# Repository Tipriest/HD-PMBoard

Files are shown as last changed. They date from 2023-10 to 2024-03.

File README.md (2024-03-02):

### 1.设计要求

1. 尺寸，30.50mm孔距
2. 电源输入: 4S-6S(14-25.2V)
3. 电源输出:
   * 直出/45A 四路
   * 12V/7.5A 一路
   * 5V/5A 一路
4. 将PMU相关的东西进行集成(5V转压+飞控供电+采样电阻+模拟信号)(CAN信号先留着，下一版再说)

### 2. 设计要求分析

1. 12V是用来给Nvidia的系列模组供电的，根据目前(2023.11.11)的各个模组的功耗情况，可以得知**Jeston AGX Origin 64GB**需要15W-60W的电源，所以保险起见需要提供12V/7.5A=90W的一路电源 *[Reference](https://www.nvidia.com/en-sg/autonomous-machines/embedded-systems/jetson-orin/)*
2. 5V是用来给飞控供电的，飞控5V/5A 一路

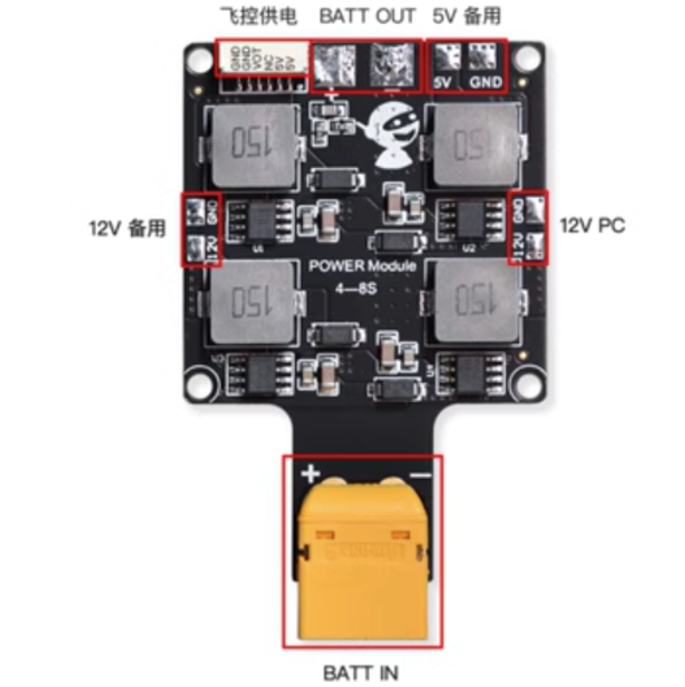
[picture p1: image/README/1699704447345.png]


3. PMU设计分析: PMU在正常情况下是这样的一个模块，其他一些名称有飞行电流计 CAN电流计 *[Reference](https://item.taobao.com/item.htm?spm=a21n57.1.0.0.57e4523cPJaut3&id=620349108685&ns=1&abbucket=3#detail)*

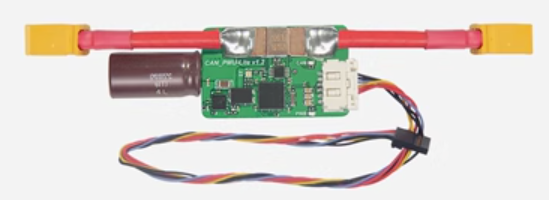
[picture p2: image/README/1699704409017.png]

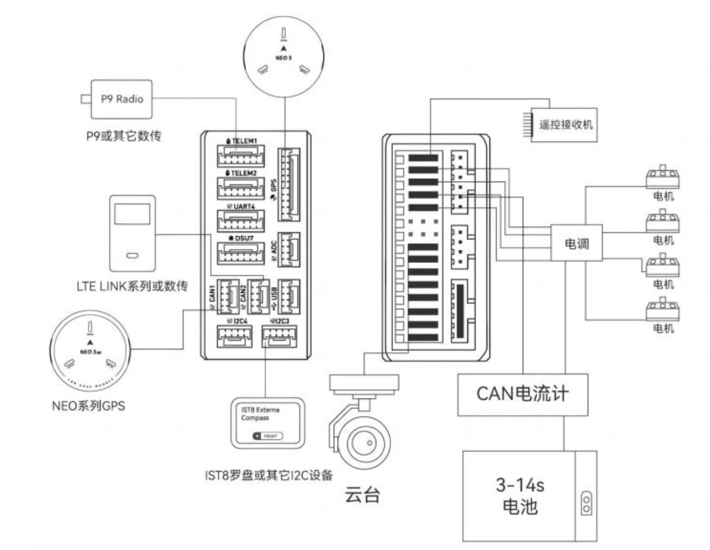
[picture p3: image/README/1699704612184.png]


> * 正常的飞控，以Nora+为例，一般会拥有两个供电的输入端口，称为PowerA和PowerC，根据下图的解释可以知道，PowerA是正常的ADC信息+供电的通道，PowerC是CAN信息+供电的通道
>
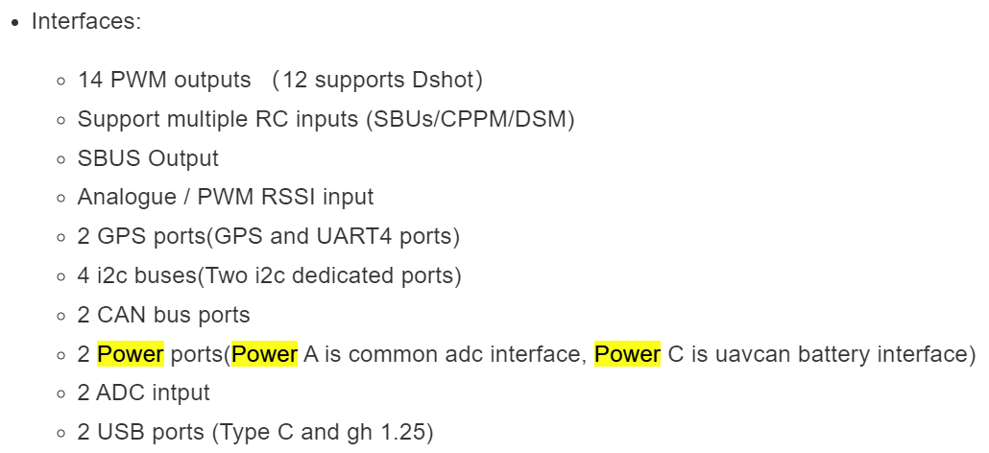
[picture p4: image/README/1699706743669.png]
> 

> * 飞控的电源输入的正常的6pin线序为下图所示，具有VOL和CUR，分别表示输入电压和输入电流
>
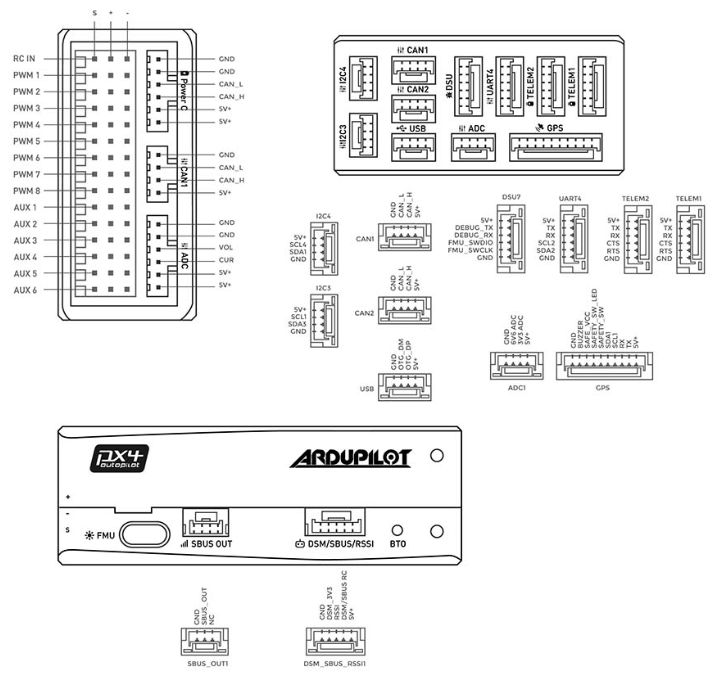
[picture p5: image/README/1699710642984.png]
> 

### 3. 方案选型

> * 采用PowerA端口，提供ADC信息
> * 电流采样: 采用0.25mr采样电阻，采用INA240A3进行100倍增益放大，输出模拟电流采样值，安培/伏特写入40
> * 电压采样: 采用OPA171AIDBVR运放，采样电源的输入电压，电压分压器写入16
>
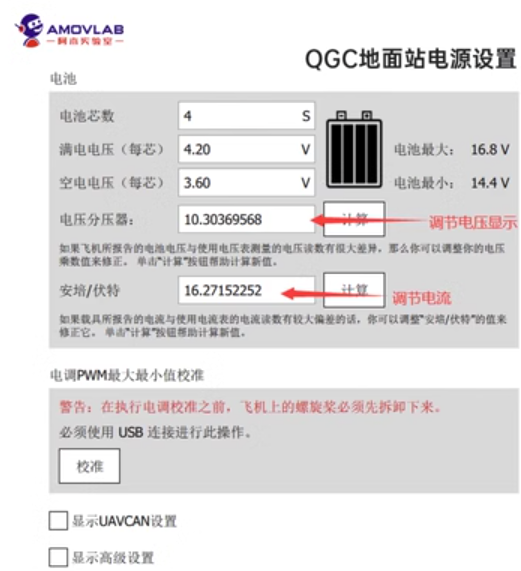
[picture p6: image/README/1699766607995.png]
> 
>
> * 分压器设计采样范围
>
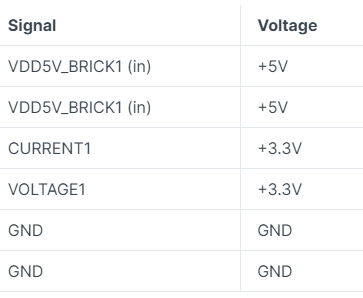
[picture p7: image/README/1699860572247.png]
> 
>
> * 转压芯片选型
>
> | 芯片名称        |      厂家      | 输入电压范围 | 输出电压范围 | 输出电流max |     优缺点     |
> | :-------------- | :------------: | :----------: | :----------: | :---------: | :-------------: |
> | LT8645SIV#PBF   |  ADI(亚德诺)  |   3.4V-65V   |   1.8V~12V   |     8A     |  49.15/片 难焊  |
> | SIC461ED-T1-GE3 |  VISHAY(威世)  |   4.5V-60V   | 800mV~55.2V |     10A     | 14.02/片 正常焊 |
> | SIC471ED-T1-GE3 |  VISHAY(威世)  |   4.5V-55V   | 800mV~50.6V |     12A     | 17.65/片 正常焊 |
> | FAN65008B       | onsemi(安森美) |   4.5V-65V   | 600mV~32.5V |     10A     |  32/片 正常焊  |
>
> * 采用SIC461ED-T1-GE3进行 **输入电压** 转 **12V** ，效率在96-97%
> * 采用SIC461ED-T1-GE3进行 **输入电压** 转 **5V** ，效率在94-95%

### 4.原理图及PCB

#### 4.1 原理图

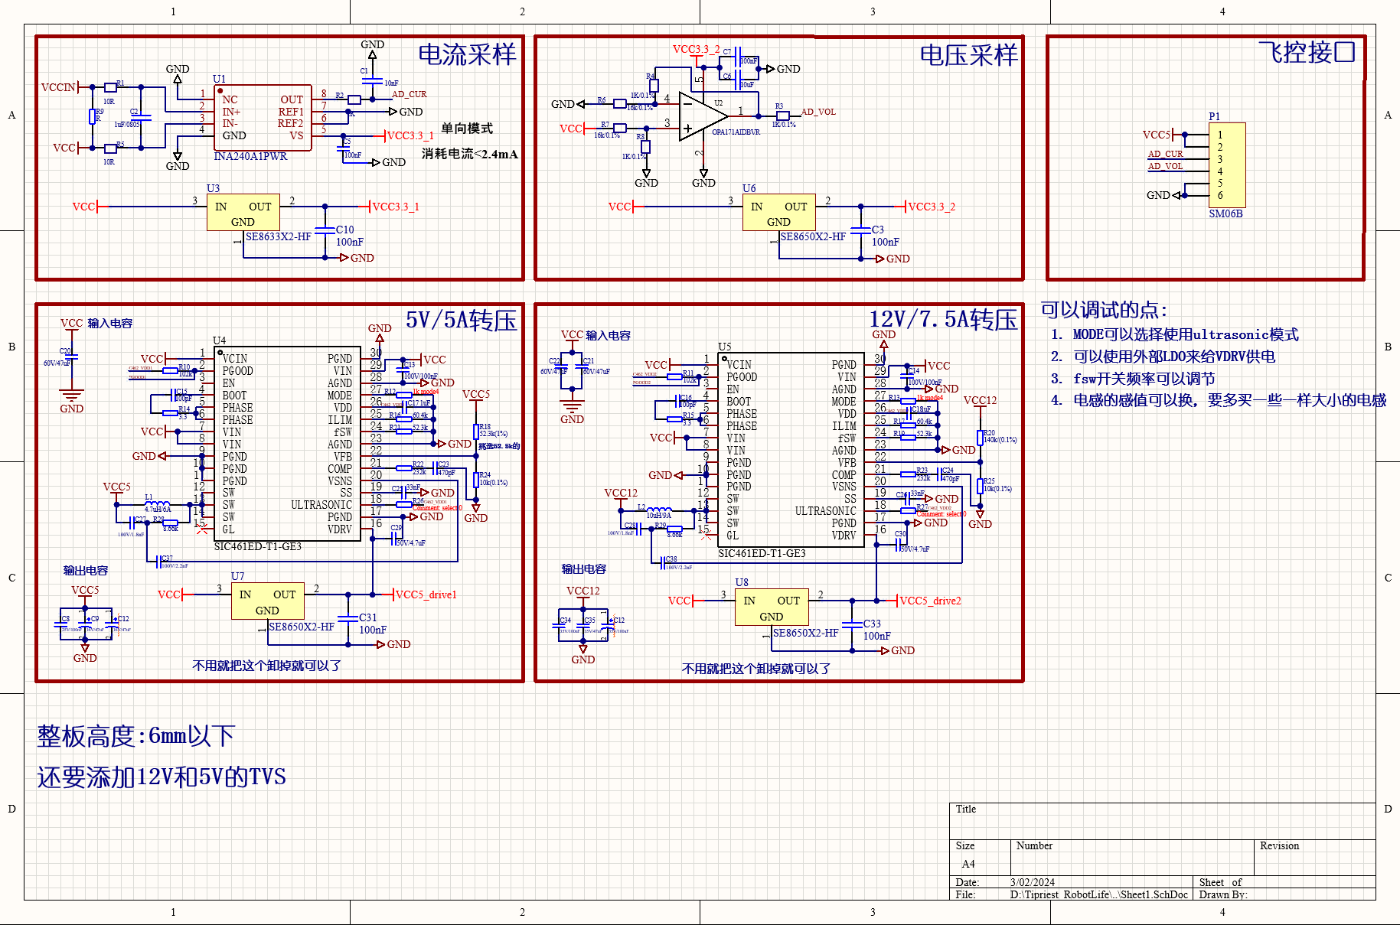
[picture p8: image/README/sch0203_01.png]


#### 4.2 PCB

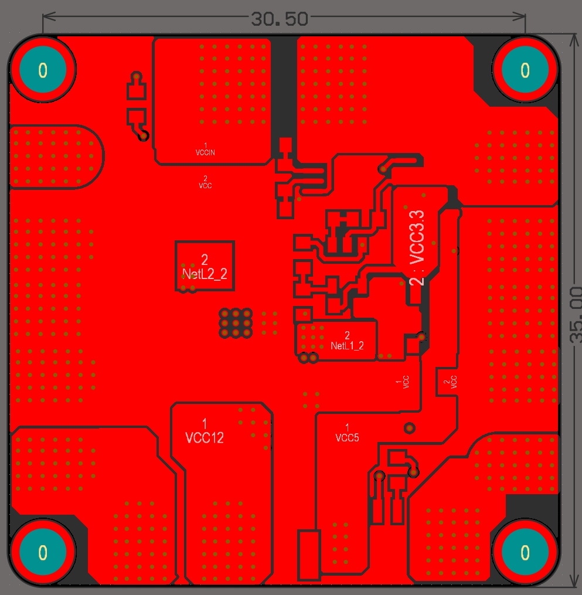
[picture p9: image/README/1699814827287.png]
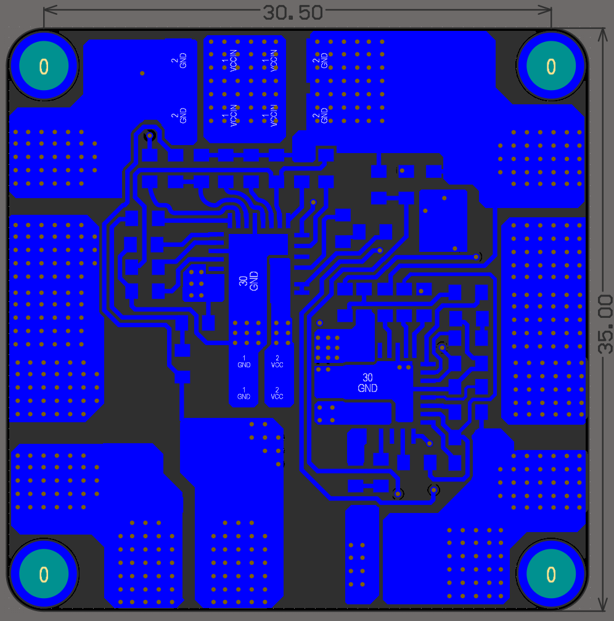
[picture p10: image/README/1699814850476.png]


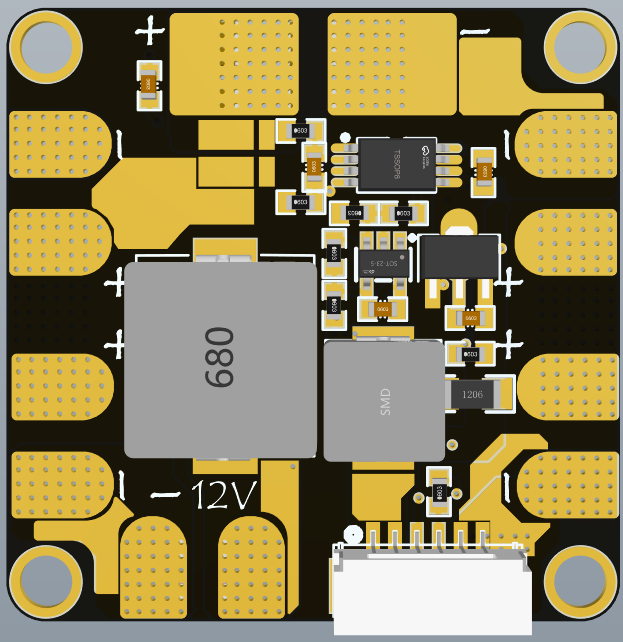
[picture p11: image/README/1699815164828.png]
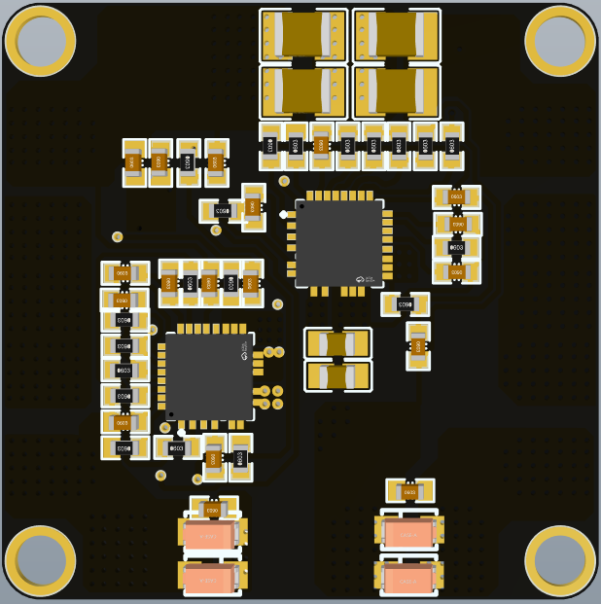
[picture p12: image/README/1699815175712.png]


### 5.待办

1. 12V转压相关的东西还要计算(12V现在的相关参数都是搬的5V的相关参数)
2. 优化一下布局，重新考虑一下布板，现在的大电流相关的东西还需要重新进行考虑
3. 在飞控引脚和12V引脚处加标注
4. 把使用注意事项写到板子的背面

### 6.测试

1. 空载，满载电压准确度
2. 空载，满载电源纹波(在满载的时候纹波在50mV以下)
3. 动态响应度(突然加载和掉载的时候)(在300mV以内可以接受)
4. 发热情况(温度越低越好，满载5min不要高于60度)
5. 效率(任意负载高于96%)
6. 加入输出的12V和5V TVS

### 7.异常测试

1. 镊子输出短路查看响应
2. 开关串联输入查看模块是否会烧毁
3. 动态响应度(突然加载和掉载的时候)(在300mV以内可以接受)
4. 发热情况(温度越低越好，满载5min不要高于50度)
5. 效率(任意负载高于96%)
6. 加入输出的12V和5V TVS

### 8.可能发生的最坏的事情

1. 12V转压故障，导致12V直出电源电压烧坏后级电脑、无人机炸机
2. 飞控6pin引脚线序画反或者接线反导致烧飞控
3. 飞控模拟电压采样出问题烧飞控
4.

### 9.使用注意

1. 5V路禁止同时给舵机或其他电机供电
2. 12V禁止同时给其他舵机或者电机供电
3.

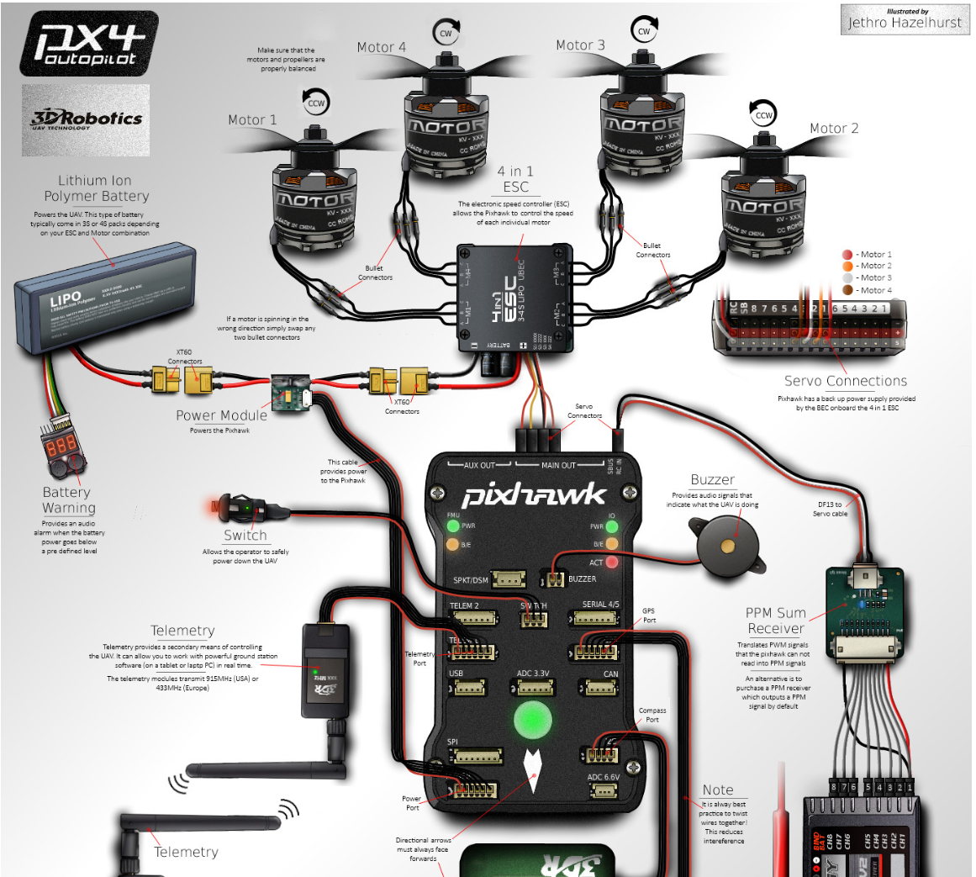
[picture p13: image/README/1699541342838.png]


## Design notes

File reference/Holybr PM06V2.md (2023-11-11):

## Holybr PM06V2

[淘宝链接](https://item.taobao.com/item.htm?spm=a21n57.1.0.0.2a8f523c6srMib&id=584871481169&ns=1&abbucket=3#detail)

#### Chip Used

LM5576 for 5V/3A output

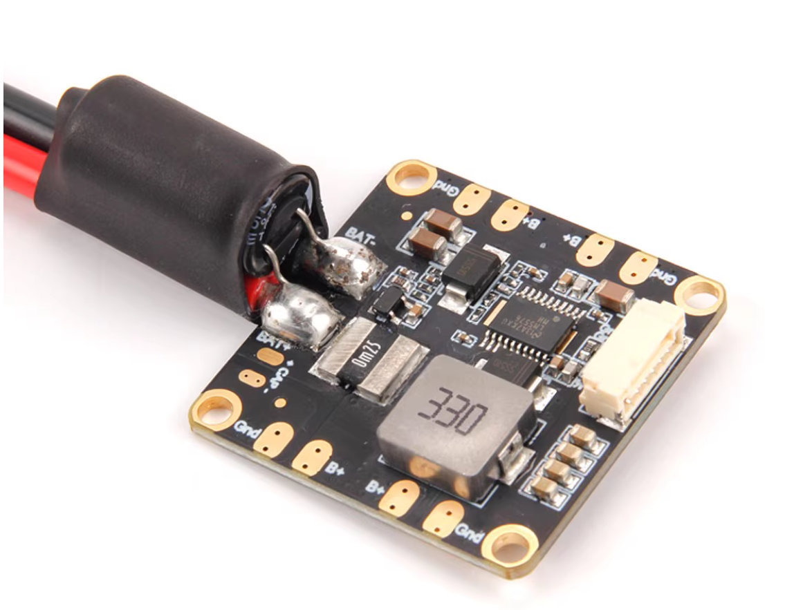
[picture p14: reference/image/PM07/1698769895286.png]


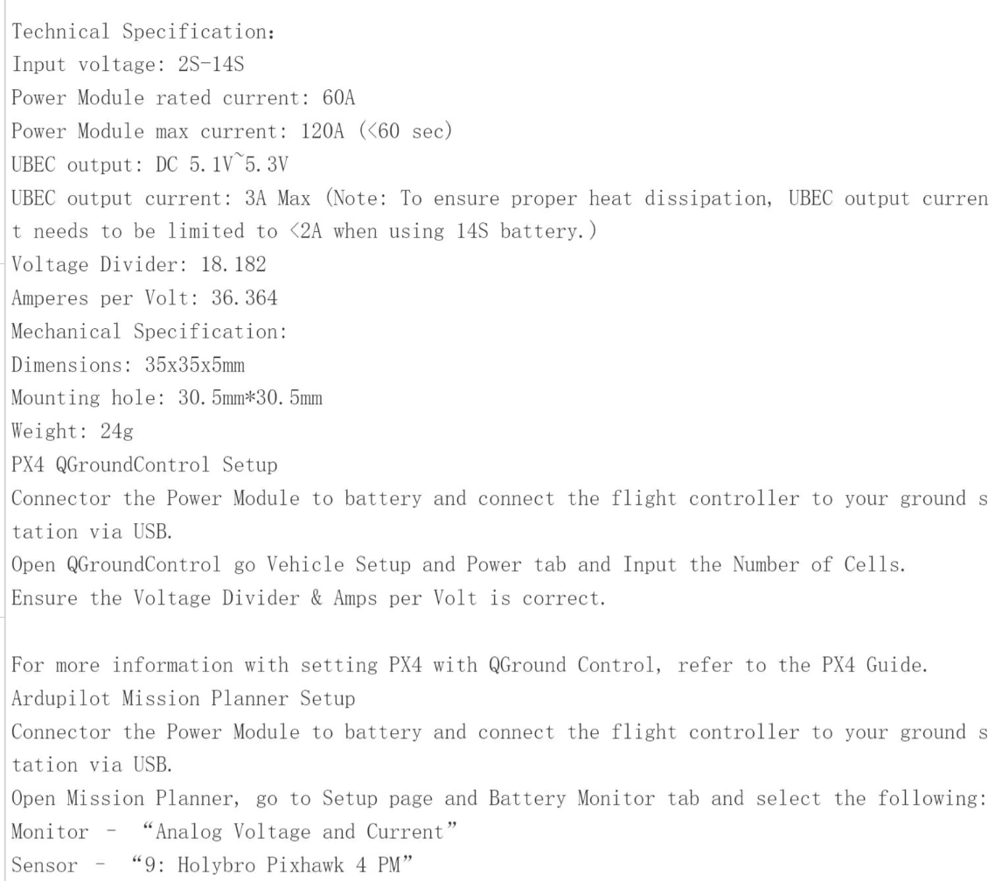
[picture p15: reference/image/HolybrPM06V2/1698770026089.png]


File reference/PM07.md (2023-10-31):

## PM07 Board

#### Chip Used

LM5576 for 5V/3A output

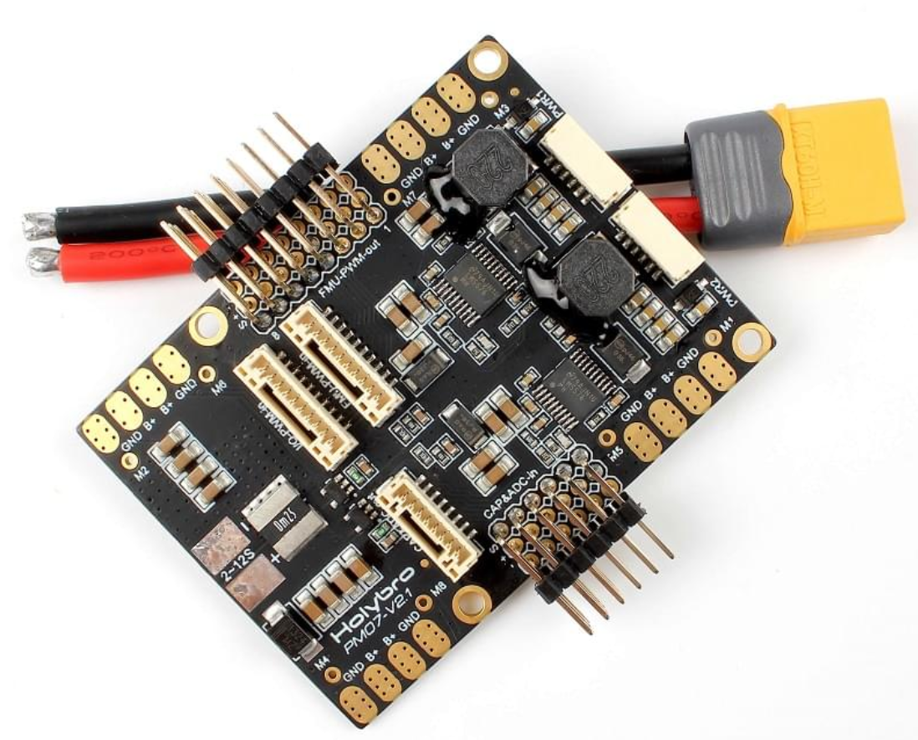
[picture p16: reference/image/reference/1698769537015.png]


[https://docs.px4.io/main/en/power_module/holybro_pm07_pixhawk4_power_module.html](https://docs.px4.io/main/en/power_module/holybro_pm07_pixhawk4_power_module.html)

* **PCB Current:** total 120A outputs (MAX)
* **UBEC 5v output current:** 3A
* **UBEC input voltage:** 2~12s LiPo
* **Dimensions:** 68 x 50 x 8 mm
* **Mounting Holes:** 45 x 45 mm
* **Weight:** 36g

## 清单内容

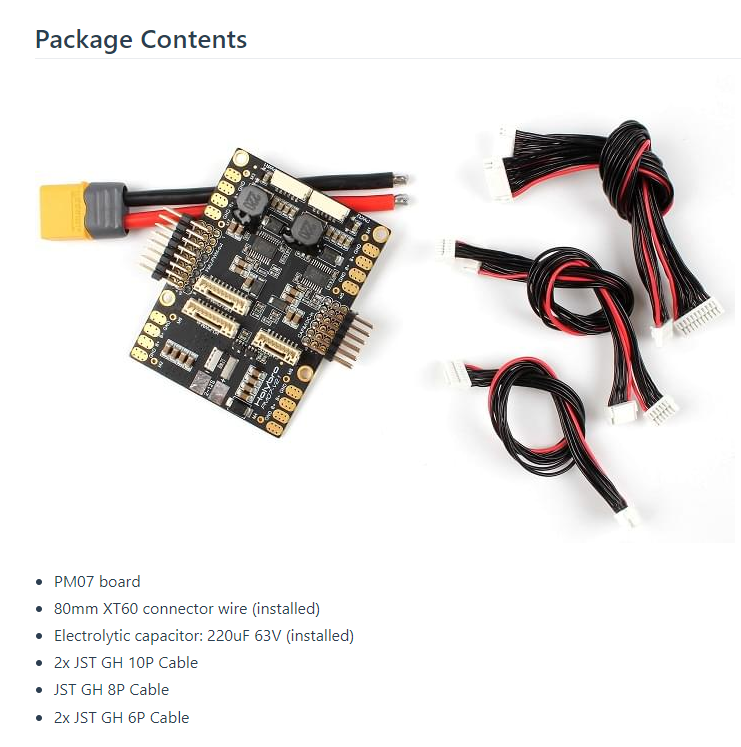
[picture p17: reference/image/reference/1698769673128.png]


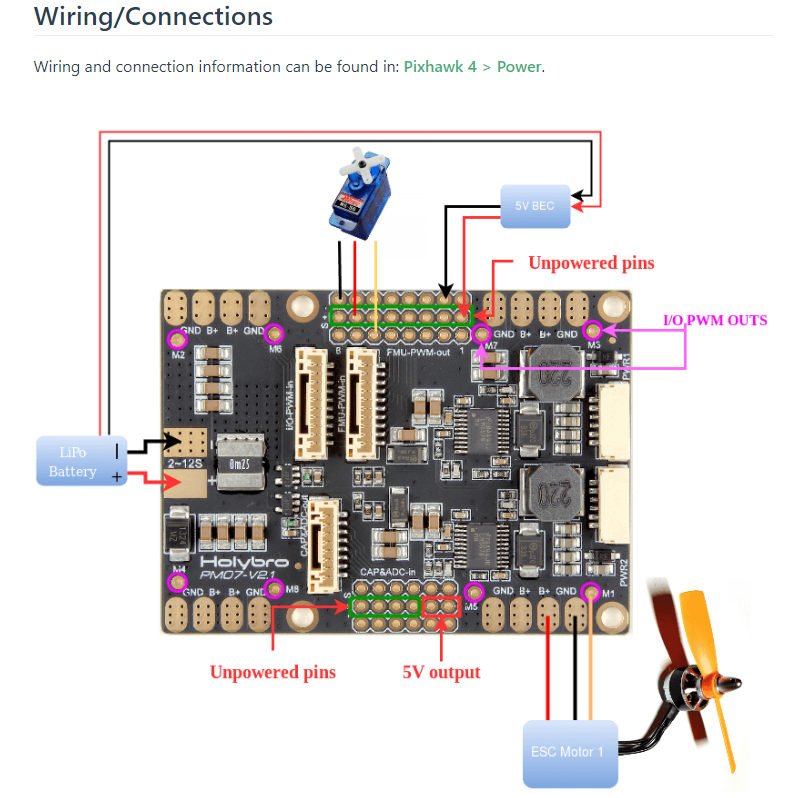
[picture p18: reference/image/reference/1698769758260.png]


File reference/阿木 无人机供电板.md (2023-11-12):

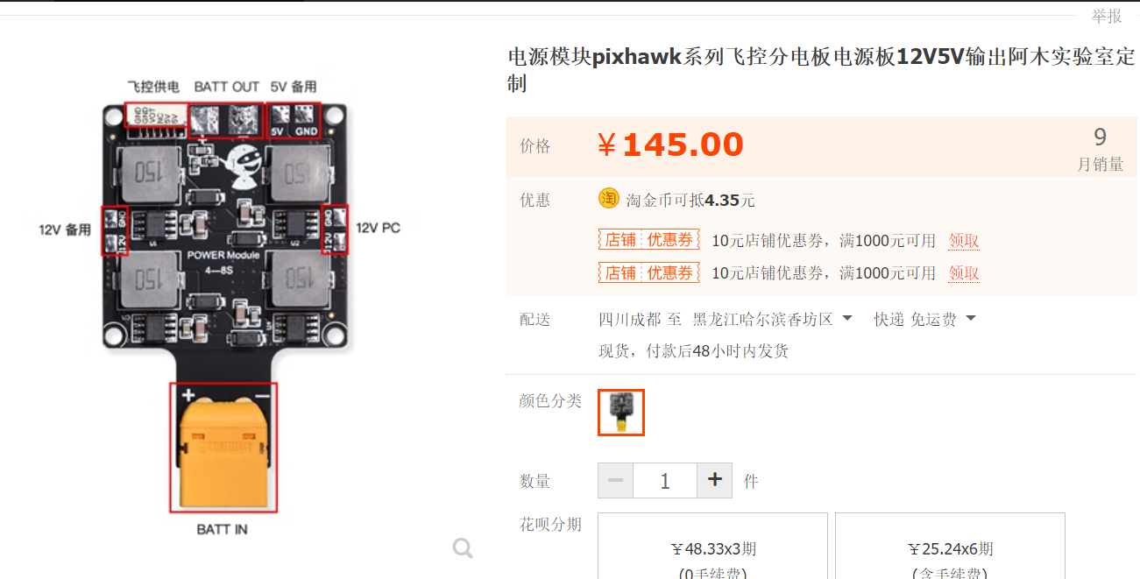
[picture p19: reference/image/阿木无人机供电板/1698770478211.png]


*[reference link](https://item.taobao.com/item.htm?spm=a1z10.5-c-s.w4002-22617251051.26.7bd372e8yRLnir&id=643870261280)*

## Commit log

2023-11-07 update the doc files
    [PCB1.PcbDoc, PCB_Project.PrjPcb, Sheet1.SchDoc]
2023-11-11 add some refs
    [PCB1.PcbDoc, PCB_Project.PrjPcb, Sheet1.SchDoc]
2023-11-12 添加选型表，梳理采样方案
2023-11-12 原理图画了一部分，加了一些PCB封装
    [PCB1.PcbDoc, Sheet1.SchDoc]
2023-11-12 add the pcb file
    [PCB_Project.PrjPcb, Sheet1.SchDoc]
2023-11-12 尝试一下markdown图片并排显示
2023-11-13 markdown图片并排显示
2024-03-02 update schdoc
    [Sheet1.SchDoc]
2024-03-02 update shcdoc and readme file
    [Sheet1.SchDoc]
2024-03-03 update schdoc and pcbdoc
    [Sheet1.SchDoc]
2024-03-17 add a capacitor of 12V
    [Sheet1.SchDoc]
